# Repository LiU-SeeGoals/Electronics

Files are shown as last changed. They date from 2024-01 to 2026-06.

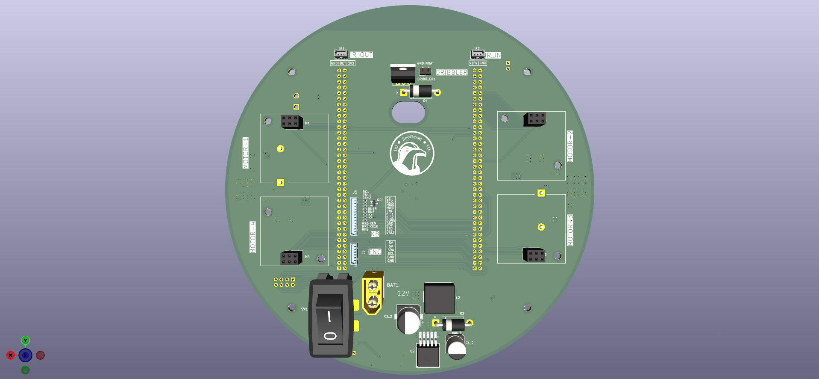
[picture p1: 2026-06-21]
pwr_v3/Docs and Images/3dRenders/pwr_v3_3dB.png

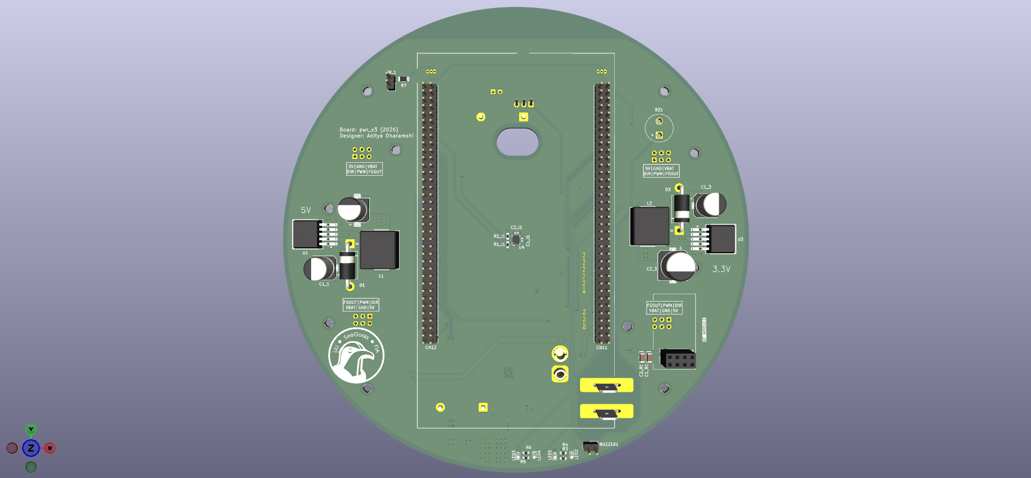
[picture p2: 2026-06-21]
pwr_v3/Docs and Images/3dRenders/pwr_v3_3dT.png

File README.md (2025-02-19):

# Electronics
Schematics etc.

# Motor driver

The motor driver has 5 important pins, 

Motor driver has 5 pins to the devboard, 2 power pins and 8 pins to the motor 

The important pins are
```
PWM, - Takes PWM signal to decide speed of motor, generate from devboard with timers.

FGOUT, - Hall sensor tick output, work like a wheel encoder and ticking as the motor spins so that we know how much the motor has spun.

nFault, - Gives fault messages when fault states are entered by going low. Currently does not work, set this pin HIGH 5v or motor driver can enter test mode.

brake - HIGH sets all motor coils high breaking the motor hard.

dir - Decides direction for motor
```

## Motor driver improvements

Capacitors and components change capacitance, inductance, etc as the voltage changes. 
This was not know during the making of driver.

Capacitors should be closer to the pins they are filtering.

There is a risk of overheating if the motors get stuck for a longer time, adding some cooling would be nice.

## Getting started

Add the .pretty library file to get footprints from lib/

Using kicad: preferences -> Manage footprint libraries

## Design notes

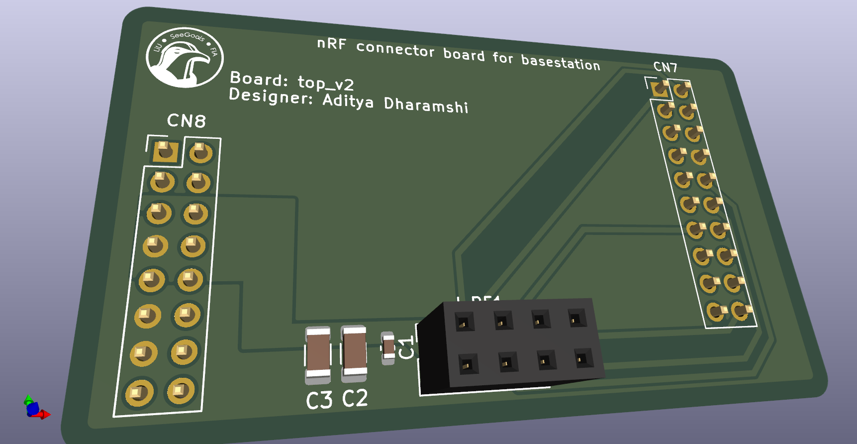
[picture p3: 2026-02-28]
top_v2/Docs and Images/top_v2_3dT2.png

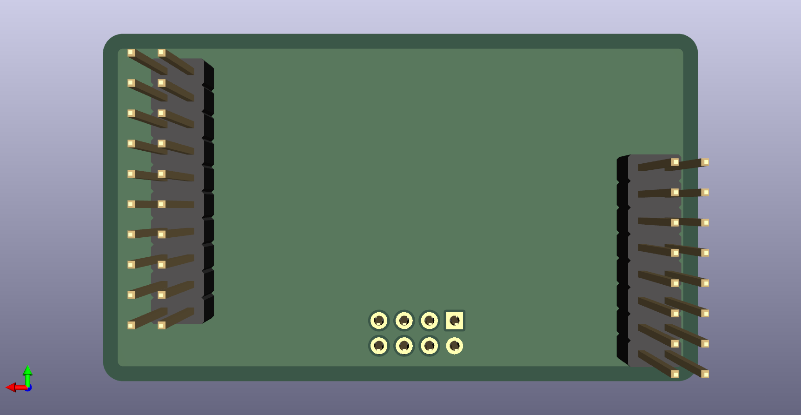
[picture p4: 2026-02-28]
top_v2/Docs and Images/top_v2_3dB.png

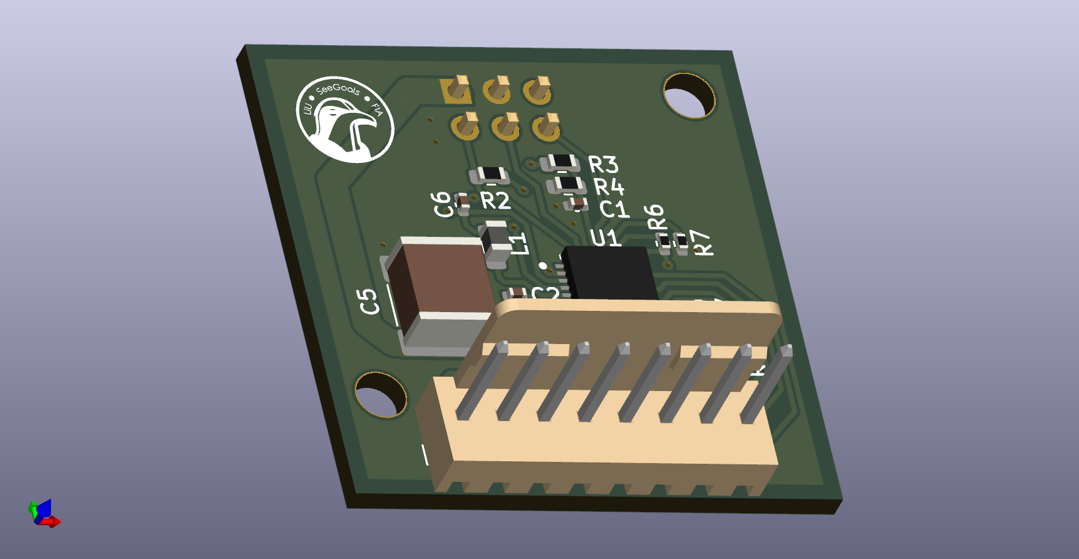
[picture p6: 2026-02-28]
md_v1/Docs and Images/md_v1_3dT2.png

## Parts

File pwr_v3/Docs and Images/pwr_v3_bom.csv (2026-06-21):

Value | Reference | Footprint | Description
Conn_01x02 | IR_1 | Connector_PinHeader_2.54mm:PinHeader_1x02_P2.54mm_Vertical | C27985187
Conn_01x02 | BUZZER1 | Connector_PinHeader_2.54mm:PinHeader_1x02_P2.54mm_Vertical | C27985187
8.2p | C1_R1 | Capacitor_SMD:C_1206_3216Metric | C3037650
Conn_02x04_Counter_Clockwise | J_RF1 | Connector_PinSocket_2.54mm:PinSocket_2x04_P2.54mm_Vertical | C2977588
D | D4 | Diode_THT:D_DO-201AD_P15.24mm_Horizontal | C2965232
1000uF | C2_1 | Capacitor_SMD:CP_Elec_8x10.5 | C2910470
LM2576S-3.3 | U3 | Package_TO_SOT_SMD:TO-263-5_TabPin3 | C2863400
LM2576S-5 | U1 | Package_TO_SOT_SMD:TO-263-5_TabPin3 | C880552
100uH | L1,L3 | Inductor_SMD:L_Sunlord_MWSA1206S-101 | C408533
1000uF | C2_2,C2_3 | Capacitor_SMD:CP_Elec_10x10.5 | C401766
150uH | L2 | Inductor_SMD:L_TaiTech_TMPC1265_13.5x12.5mm | C357258
100nF | C1_I1 | Capacitor_SMD:C_0402_1005Metric | C307331
1k | R2_I1 | Resistor_SMD:R_0603_1608Metric | C161809
1k | R1_I1 | Resistor_SMD:R_0603_1608Metric | C161809
100uF | C1_1,C1_2,C1_3 | Capacitor_SMD:CP_Elec_8x10 | C116241
XT60 | BAT1 | Connector_AMASS:AMASS_XT60-M_1x02_P7.20mm_Vertical | C98733
Buzzer | BZ1 | Buzzer_9mm_P5_D1p95:Buzzer_9mm_P5_D1p95 | C96102
Conn_02x03_Counter_Clockwise | M1,M2,M3,M4 | Connector_PinSocket_2.54mm:PinSocket_2x03_P2.54mm_Vertical | C92272
BSS84 | Q2 | Package_TO_SOT_SMD:SOT-23 | C82079
BUK9832-55A | Q1 | Package_TO_SOT_THT:TO-220-3_Vertical | C38774
10k | RK9,RK10 | Resistor_SMD:R_0402_1005Metric | C25531
100 | RK1,RK5,RK6,RK7,RK8,RK11,RK12,RK13 | Resistor_SMD:R_0402_1005Metric | C25076
62 | R3 | Resistor_SMD:R_0603_1608Metric | C23222
16.2 | R4,R6 | Resistor_SMD:R_0603_1608Metric | C22811
15.4 | R5 | Resistor_SMD:R_0603_1608Metric | C22805
100 | R7 | Resistor_SMD:R_1206_3216Metric | C242479
LM2576S-12 | U2 | Package_TO_SOT_SMD:TO-263-5_TabPin3 | C16671
1N5821 | D1,D2,D3 | Diode_THT:D_DO-201AD_P15.24mm_Horizontal | C9119
WHITE LED | LED3 | LED_SMD:LED_0603_1608Metric | C2290
BLUE LED | LED2,LED4 | LED_SMD:LED_0603_1608Metric | C2288
RED LED | LED1 | LED_SMD:LED_0603_1608Metric | C2286
100nF | C2_I1 | Capacitor_SMD:C_0402_1005Metric | C307331
LSM6DSLTR | U4 | lsm6dsltr:LGA-14_3x2.5mm_P0.5mm_LayoutBorder3x4y | C126672
10uF | C2_R1 | Capacitor_SMD:C_1206_3216Metric | C1849

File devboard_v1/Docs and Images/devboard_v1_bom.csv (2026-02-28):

Designator | Footprint | Quantity | Value | LCSC Part #
C1, C10, C16, C27, C30, C31 | 402 | 6 | 4.7uF | C23733
C11 | 402 | 1 | 1uF | C1525
C12, C13, C14, C15, C17, C18, C19, C2, C20, C21, C22, C23, C3, C4, C5, C6, C7, C8, C9 | 402 | 19 | 100nF | C14445
C24, C25, C26 | 402 | 3 | 2.2uF | C107369
C28, C29 | 402 | 2 | 10uF | C315248
D1 | 603 | 1 | LED | C2286
IC1 | SON95P300X300X100-7N-D | 1 | ST1L05CPU33R | C2969933
R1 | 402 | 1 | 62 | C412968
R2 | 402 | 1 | 10k | C71617
R3 | 402 | 1 | 100k | C191569
SW1 | TPS645-5NC105_JLCPCB | 1 | CK_KMS2xxG | C19191549
U1 | LQFP-144_20x20mm_P0.5mm | 1 | STM32H755ZITx | C730212

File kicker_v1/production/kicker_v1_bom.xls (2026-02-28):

Comment | Designator | Footprint | JLCPCB Part#(optional)
R1206 | R19 | R1206 | C873620
C1210 | C12,C13,C15,C16,C17 | C1206 | C13585
SMD | C11 | SMD | C178594
R0603 | R6,R8,R10,R20 | R0603 | C402972
R1206 | R21,R22 | R1206 | C17903
R1206 | R14 | R1206 | C17963
R0603 | R9,R13 | R0603 | C403101
R0603 | R2,R11,R15 | R0603 | C98220
R0603 | R1,R4,R12,R17 | R0603 | C22548
SOIC8N | Q1 | SOIC8N | C455164
CHIP-LED0603 | LED1 | CHIP-LED0603 | C6848499
L0603 | L2,L4,L5 | L0603 | C14709
SOIC8N | IC8 | SOIC8N | C903505
SOIC8N | IC6 | SOIC8N | C7377
SOT23 | IC4 | SOT23 | C150830
MSOP8 | IC3 | MSOP8 | C2861303
1206 | F1 | 1206 | C3163312
SMB | D2,D3 | SMB | C135043
SMC | D1 | SMC | C241736
C0805 | C21 | C0805 | C1710
C0603 | C20,C24,C25 | C0603 | C3833060
C0603 | C6,C7,C8,C9,C10,C18,C19,C22,C27 | C0603 | C1591
DF13-12P-1.25V | X1 | DF13C-12P-1.25V | C5340794
0R008 | R18 | R1206 | C912775
4R7 | R16 | R0805 | C278658
IKB40N65ES5 | Q2,Q3 | D2PAK | C536153
rd | LED2 | CHIP-LED0603 | C6784992
MCP1790 | IC10 | SOT223 | C511289
LT3751FE | IC7 | TSSOP20P | C580130
SI8620EC-B-IS | IC1 | SOIC8N | C7424691
DSEP40-03AS-TRL | D4,D5 | D2PAK | C17389077

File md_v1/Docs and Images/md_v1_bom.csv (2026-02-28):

Reference | Value | Footprint | Description
C1 | 100nF | Capacitor_SMD:C_0402_1005Metric | C1525
C2 | 47nF | Capacitor_SMD:C_0402_1005Metric | C307339
C3 | 1uF | Capacitor_SMD:C_0402_1005Metric | C14445
C4 | 0u1F | Capacitor_SMD:C_0402_1005Metric | C307331
C5 | 22uF | Capacitor_SMD:C_2220_5750Metric | C784103
C6 | 22uF | Capacitor_SMD:C_0402_1005Metric | C105226
C7 | 1uF | Capacitor_SMD:C_0402_1005Metric | C76999
L1 | 47uH | Inductor_SMD:L_0805_2012Metric | C105499
POWER1 | Conn_02x03_Odd_Even | Connector_PinHeader_2.54mm:PinHeader_2x03_P2.54mm_Vertical | C7430399
R1 | 5k1 | Resistor_SMD:R_0603_1608Metric | C403509
R2 | 5k1 | Resistor_SMD:R_0603_1608Metric | C403509
R3 | 27k | Resistor_SMD:R_0603_1608Metric | C22967
R4 | 20k | Resistor_SMD:R_0603_1608Metric | C4184
R5 | 1M | Resistor_SMD:R_0805_2012Metric | C107700
R6 | 47k | Resistor_SMD:R_0402_1005Metric | C25792
R7 | 22k | Resistor_SMD:R_0402_1005Metric | C25547
U1 | MCT8316Z0TRGFR | MotorDriver:RGF0040E-IPC_A | C3681342

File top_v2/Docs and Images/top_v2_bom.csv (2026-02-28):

Designator | Footprint | Quantity | Value | LCSC Part #
C1 | 603 | 1 | 8.2pF | C71660
C2 | 1206 | 1 | 0.1uF | C2981728
C3 | 1206 | 1 | 10uF | C696375

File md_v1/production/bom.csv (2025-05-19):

Designator | Footprint | Quantity | Value | LCSC Part #
C1 | 0402 | 1 | 100nF
C2 | 0402 | 1 | 47nF
C3, C7 | 0402 | 2 | 1uF
C4 | 0402 | 1 | 0u1F
C5 | 2220 | 1 | 22uF
C6 | 0402 | 1 | 22uF
L1 | 0805 | 1 | 47uH
MH1, MH2 |  | 2
R1, R2 | 0603 | 2 | 5k1
R3 | 0603 | 1 | 27k
R4 | 0603 | 1 | 20k
R5 | 0805 | 1 | 1M
R6 | 0402 | 1 | 47k
R7 | 0402 | 1 | 22k
U1 | RGF0040E-IPC_A | 1 | MCT8316Z0TRGFR

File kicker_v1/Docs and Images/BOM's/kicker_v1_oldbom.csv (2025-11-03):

Reference | Value | Footprint | Qty | Digi-Key | Mfg Part #
R19 | 10M | Kicking Device v13b:R1206 | 1 | 541-10MBACT-ND
C23,C26 | 1800u | Kicking Device v13b:EB35D | 2 | 493-7224-ND
C12,C13,C15,C16,C17 | 10u | Kicking Device v13b:C1210 | 5 | 1276-6736-2-ND | C3225X5R1H106M250AB
C11 | 220u | Kicking Device v13b:PANASONIC_F | 1 | PCE5025CT-ND | EEEFT1H221AP
R6,R8,R10,R20 | 133k | Kicking Device v13b:R0603 | 4 | P133KDBCT-ND
X1 | DF13-12P-1.25V | Kicking Device v13b:DF13C-12P-1.25V | 1 | H121957CT-ND
R21,R22 | 10 | Kicking Device v13b:R1206 | 2
R18 | 0R008 | Kicking Device v13b:R1206 | 1 | RHM.008ALCT-ND
R16 | 4R7 | Kicking Device v13b:R0805 | 1 | RHM4.7KCT-ND
R14 | 24 | Kicking Device v13b:R1206 | 1
R9,R13 | 24k9 | Kicking Device v13b:R0603 | 2 | P24.9KHCT-ND
R2,R11,R15 | 10k | Kicking Device v13b:R0603 | 3 | 311-10.0KHRCT-ND
R1,R4,R12,R17 | 1k | Kicking Device v13b:R0603 | 4 | 311-1.00KHRCT-ND
Q2,Q3 | IKB40N65ES5 | Kicking Device v13b:D2PAK | 2 | IKB40N65ES5ATMA1CT-ND
Q1 | FDS2582 | Kicking Device v13b:SOIC8N | 1 | FDS2582CT-ND
LED2 | rd | Kicking Device v13b:CHIP-LED0603 | 1 | 732-4979-1-ND
LED1 | gr | Kicking Device v13b:CHIP-LED0603 | 1 | 732-4980-1-ND
L3 | DA2034-AL | Kicking Device v13b:DA2034-AL | 1 |  | DA2034-AL
L2,L4,L5 | 120R | Kicking Device v13b:L0603 | 3 | 490-1037-1-ND
IC10 | MCP1790 | Kicking Device v13b:SOT223 | 1 | MCP1790-3302E/DB-ND
IC8 | FAN3229TMX | Kicking Device v13b:SOIC8N | 1 | FAN3229TMXCT-ND
IC7 | LT3751FE | Kicking Device v13b:TSSOP20P | 1 | LT3751EFE#PBF-ND
IC6 | MCP6002 | Kicking Device v13b:SOIC8N | 1 | MCP6002T-I/SNCT-ND
IC4 | MCP9701A | Kicking Device v13b:SOT23 | 1 | MCP9701AT-E/TTCT-ND
IC3 | ADC122S051 | Kicking Device v13b:MSOP8 | 1 | ADC122S051CIMM/NOPBCT-ND
IC1 | SI8620EC-B-IS | Kicking Device v13b:SOIC8N | 1 | 336-2062-5-ND
F1 | 8A slow | Kicking Device v13b:1206 | 1 | 507-1194-1-ND
D4,D5 | MBRB40250TG | Kicking Device v13b:D2PAK | 2 | MBRB40250TGOS-ND
D2,D3 | SMBJ13CA | Kicking Device v13b:SMB | 2 | SMBJ13CA-FDICT-ND
D1 | ES3J | Kicking Device v13b:SMC | 1 | ES3JCT-ND
C21 | 10n | Kicking Device v13b:C0805 | 1
C20,C24,C25 | 10u | Kicking Device v13b:C0603 | 3 | 490-12737-1-ND
C6,C7,C8,C9,C10,C18,C19,C22,C27 | 100n | Kicking Device v13b:C0603 | 9 | 1292-1397-1-ND

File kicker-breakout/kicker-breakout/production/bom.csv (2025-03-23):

Designator | Footprint | Quantity | Value | LCSC Part #
J1 | Molex_KK-254_AE-6410-04A_1x04_P2.54mm_Vertical | 1 | 1x04_P2.54mm
J2 | Molex_KK-254_AE-6410-08A_1x08_P2.54mm_Vertical | 1 | 1x08_P2.54mm
J3 | Hirose_DF13C_CL535-0412-6-51_1x12-1MP_P1.25mm_Vertical | 1 | DF13C_CL535-0412-6-51_1x12-1MP_P1.25mm_Vertical
Q1 | SOT-23 | 1 | BSS84
RN7A1, RN7B1, RN7C1, RN7D1, RN8A1, RN8B1, RN8C1, RN8D1 | 0805 | 8 | 100
RN9A1, RN9D1 | 0805 | 2 | 10k

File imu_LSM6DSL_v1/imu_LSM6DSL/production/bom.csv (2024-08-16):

Designator | Footprint | Quantity | Value | LCSC Part #
C1, C2 | CAP_GRM155_MUR | 2 | 100nF
D1 | 0805 | 1 | LED
J1 | PinHeader_1x02_P2.54mm_Vertical | 1 | Conn_01x02
J2 | PinHeader_1x06_P2.54mm_Vertical | 1 | Conn_01x06
R-led1 | 0603 | 1 | 470
R_scl1, R_sda1 | 1206_PAN | 2 | 1k
U1 | QFN_6DSLTR_STM | 1 | LSM6DSLTR

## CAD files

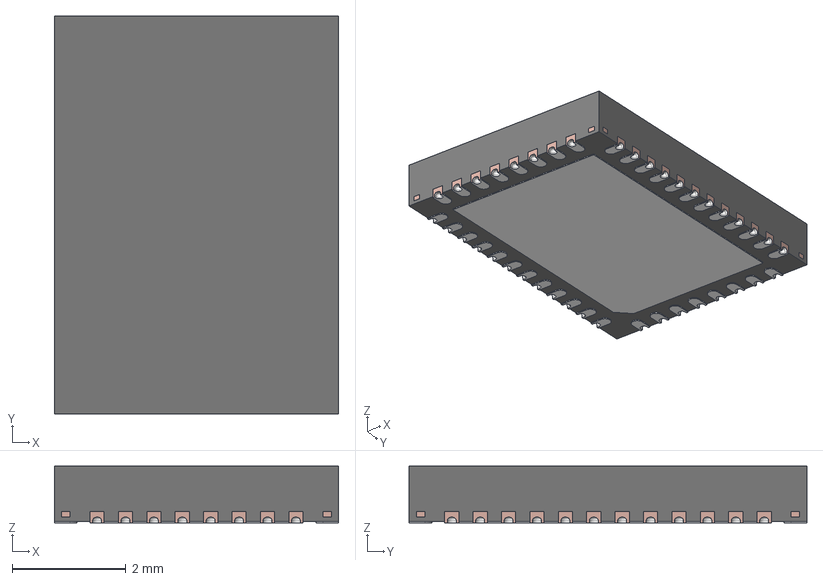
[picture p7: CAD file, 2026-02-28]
pwr_v3/libaray/motorDriver/MCT8316Z0TQRGFRQ1.stp
5.00 x 7.00 x 1.00 mm
FRAME

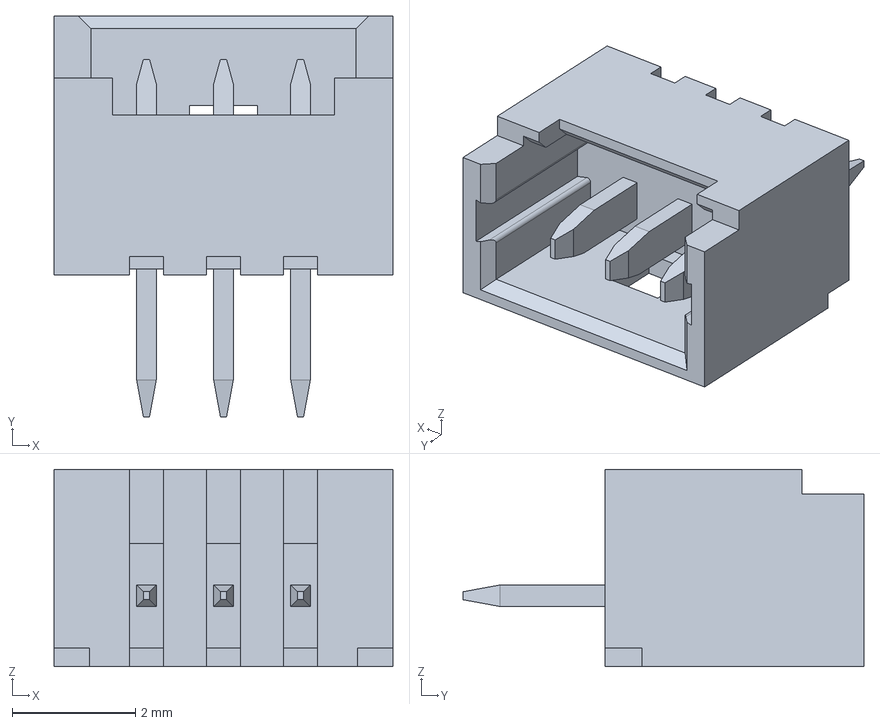
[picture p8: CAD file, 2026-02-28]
pwr_v3/libaray/picoblade_3p.stp
5.50 x 6.50 x 3.20 mm

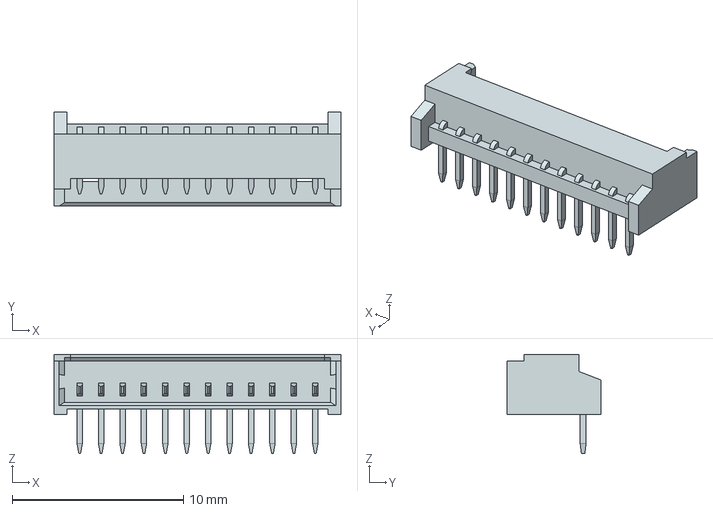
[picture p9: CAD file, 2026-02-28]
pwr_v3/libaray/picoblade_12p.stp
16.8 x 5.50 x 5.80 mm

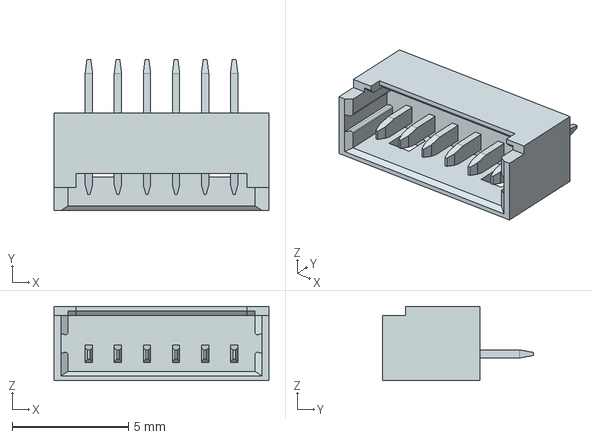
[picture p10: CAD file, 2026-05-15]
pwr_v3/libaray/530470610_6p/530470610.stp
9.25 x 6.50 x 3.20 mm

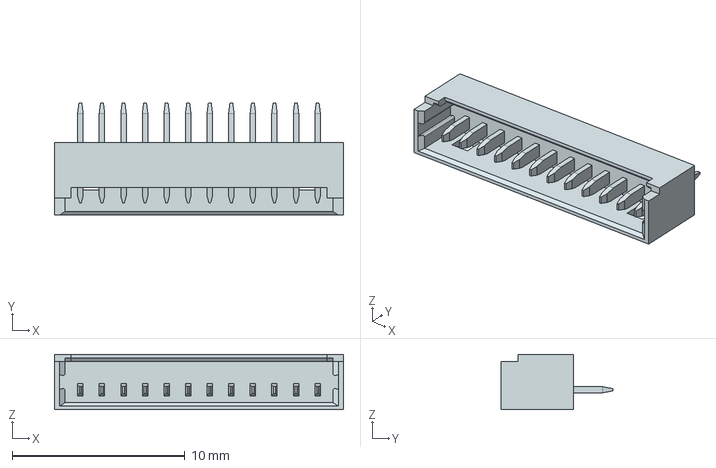
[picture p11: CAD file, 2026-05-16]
pwr_v3/libaray/530471210_12p/530471210.stp
16.8 x 6.50 x 3.20 mm

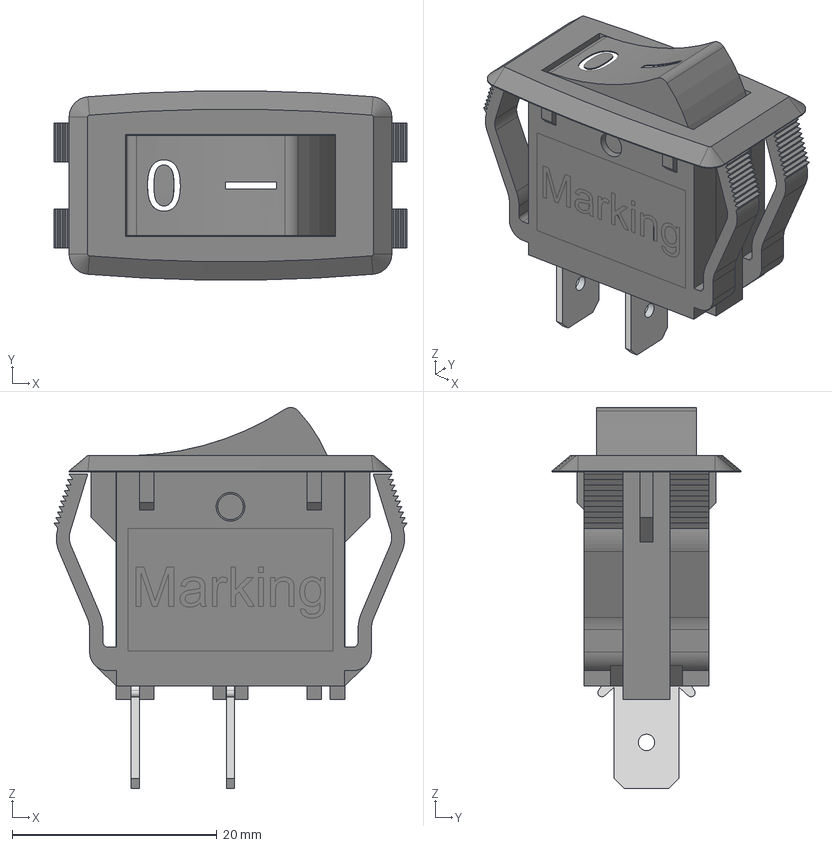
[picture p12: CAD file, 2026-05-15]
pwr_v3/libaray/Switch_471005264152/471005264152 (rev1).stp
34.5 x 18.5 x 37.2 mm
Frame
Actuator
Terminal x 2

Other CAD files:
pwr_v2/libaray/Switch_471005264152/471005264152 (rev1).stp

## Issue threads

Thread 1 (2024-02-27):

Kicker seems to be killing devboards

r0x57n, 2024-02-27:
Could be the buck converter, should have to be a list of debug steps and do some test.

r0x57n, 2024-03-28:
Got kicker up and running again on the testing board, should still make a list of debug steps to see when a board dies.

r0x57n, 2024-07-14:
seems to be working after we redid the "testboard"

Closed 2024-07-14.

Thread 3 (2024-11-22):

PCB Rev-2 modifications.

adidh4, 2024-11-22:
1. Remove the RF socket and IMU.
2. Kicker board socket and battery sockets - shift to bottom side.
3. Replace M2 with M5, and try to debug M2.
4. Add silk labels to motor driver sockets and buck convertors.
5. Increase the 0 ohm resistor sizes, probably to 1206.
6. Add mounting holes for nucleo board.
7. New locations for the robot mounting holes.
8. Add some status LED's.
9. Add new dribbler motor circuit.
10. IR sensor minor placement modification and add a current limiter resistor.

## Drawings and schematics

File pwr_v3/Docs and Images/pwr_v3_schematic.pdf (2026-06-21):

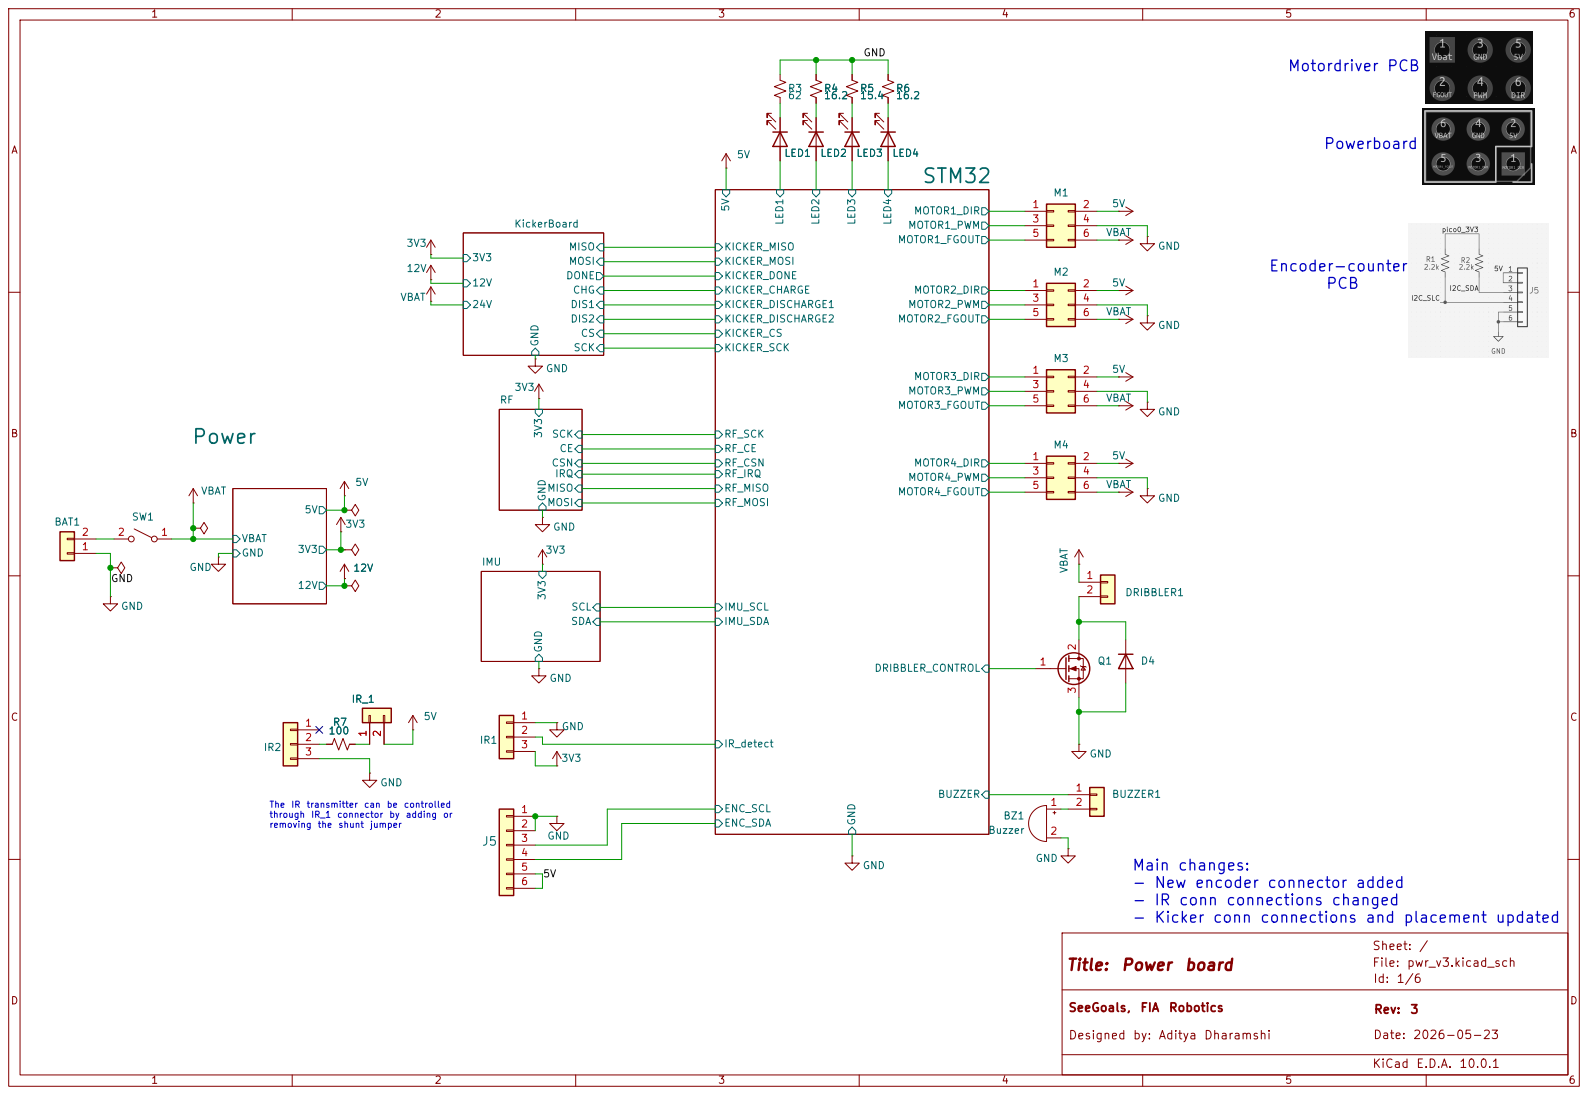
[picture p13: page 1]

SeeGoals, FIA Robotics 3V3 GND

The IR transmitter can be controlled
through IR_1 connector by adding or
removing the shunt jumper

Main changes: - New encoder connector added - IR conn connections changed - Kicker conn connections and placement updated

Designed by: Aditya Dharamshi

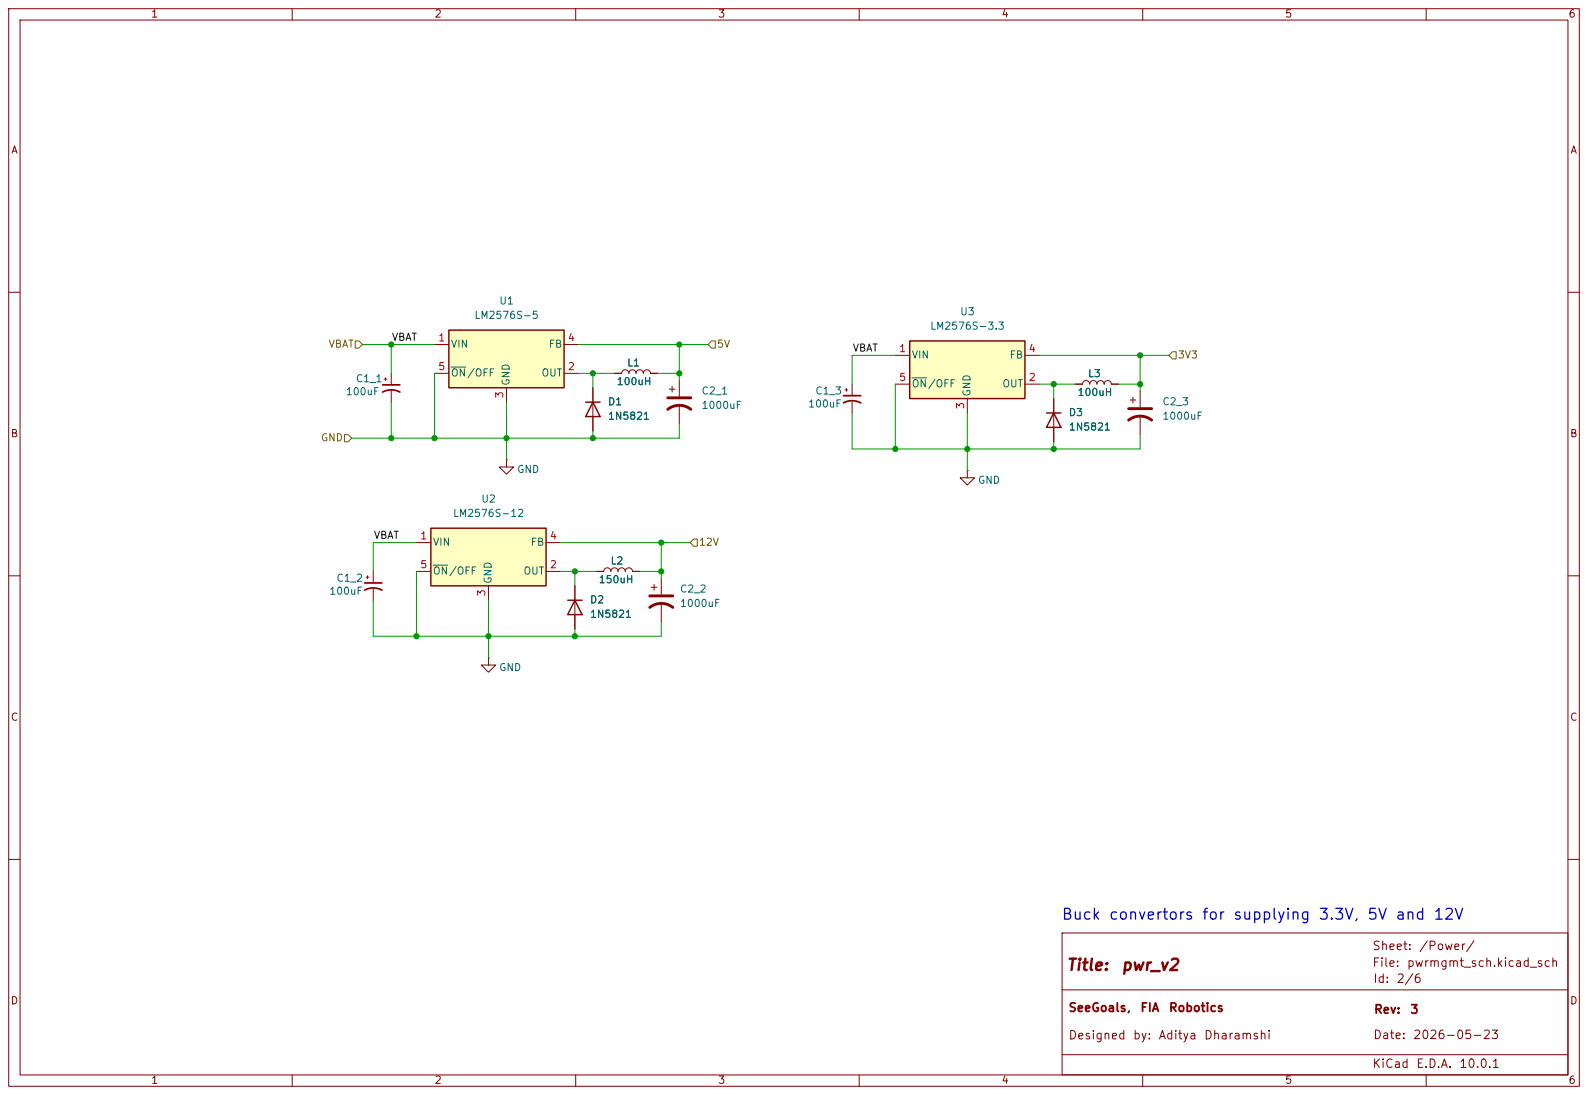
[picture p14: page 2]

Designed by: Aditya Dharamshi

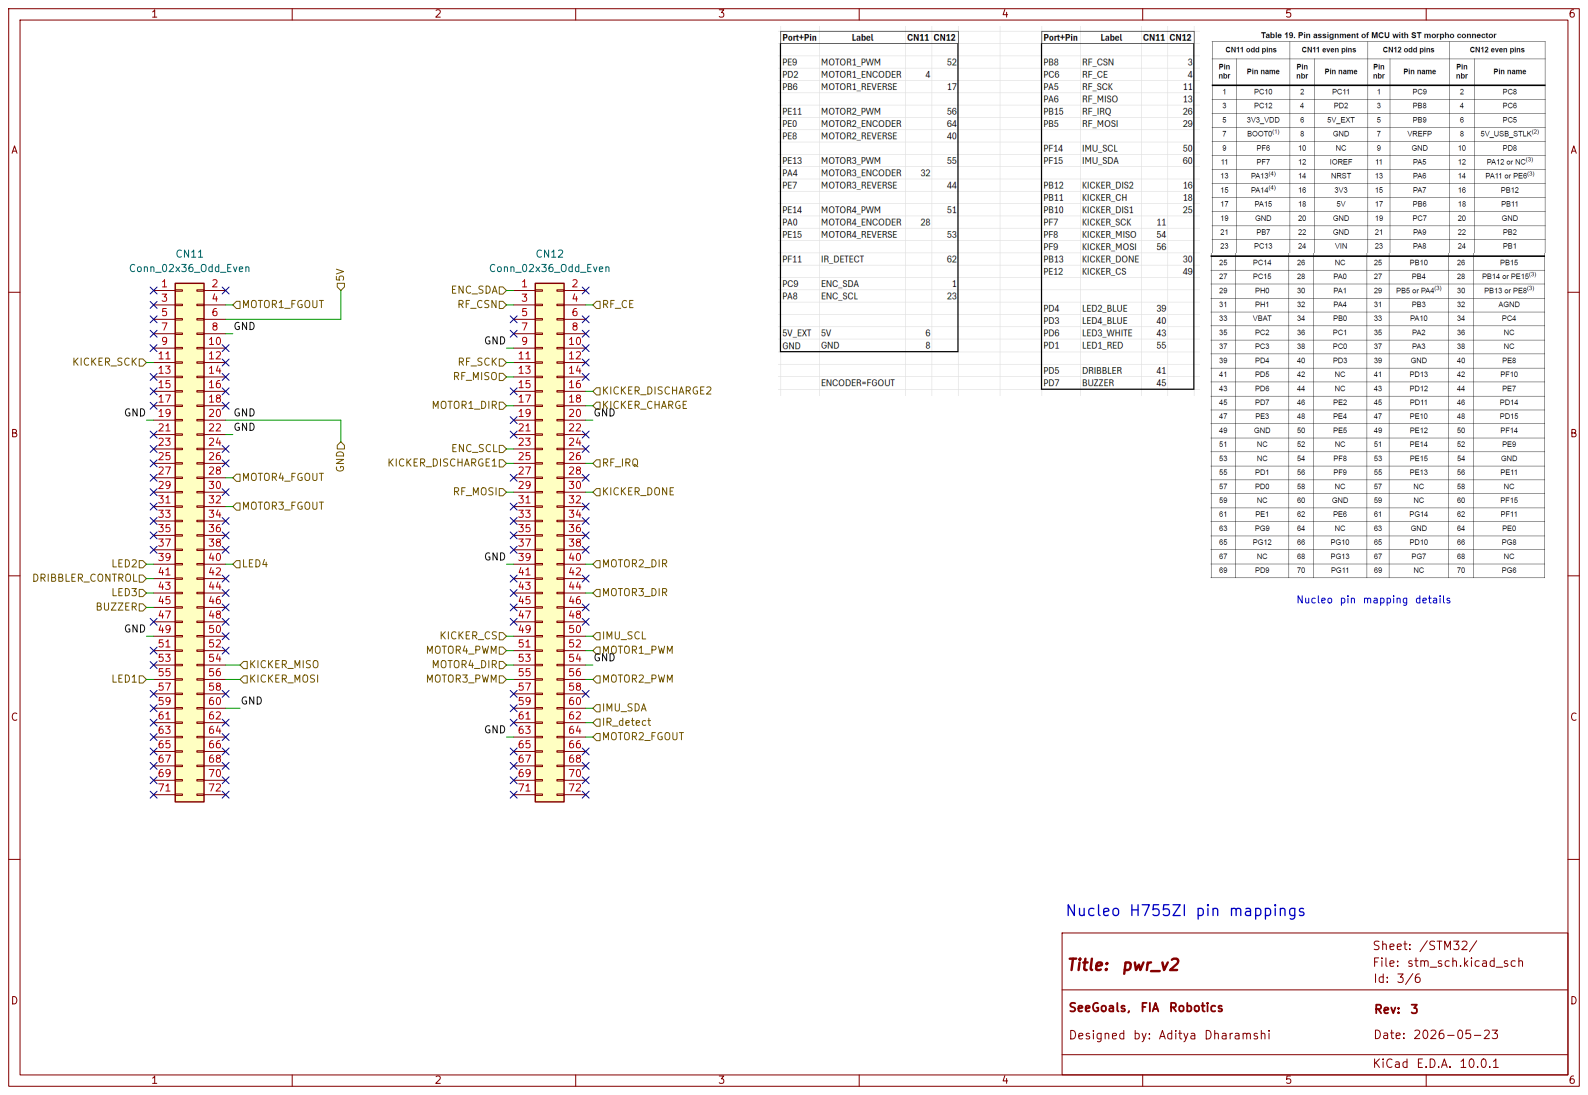
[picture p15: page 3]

Nucleo pin mapping details

Designed by: Aditya Dharamshi

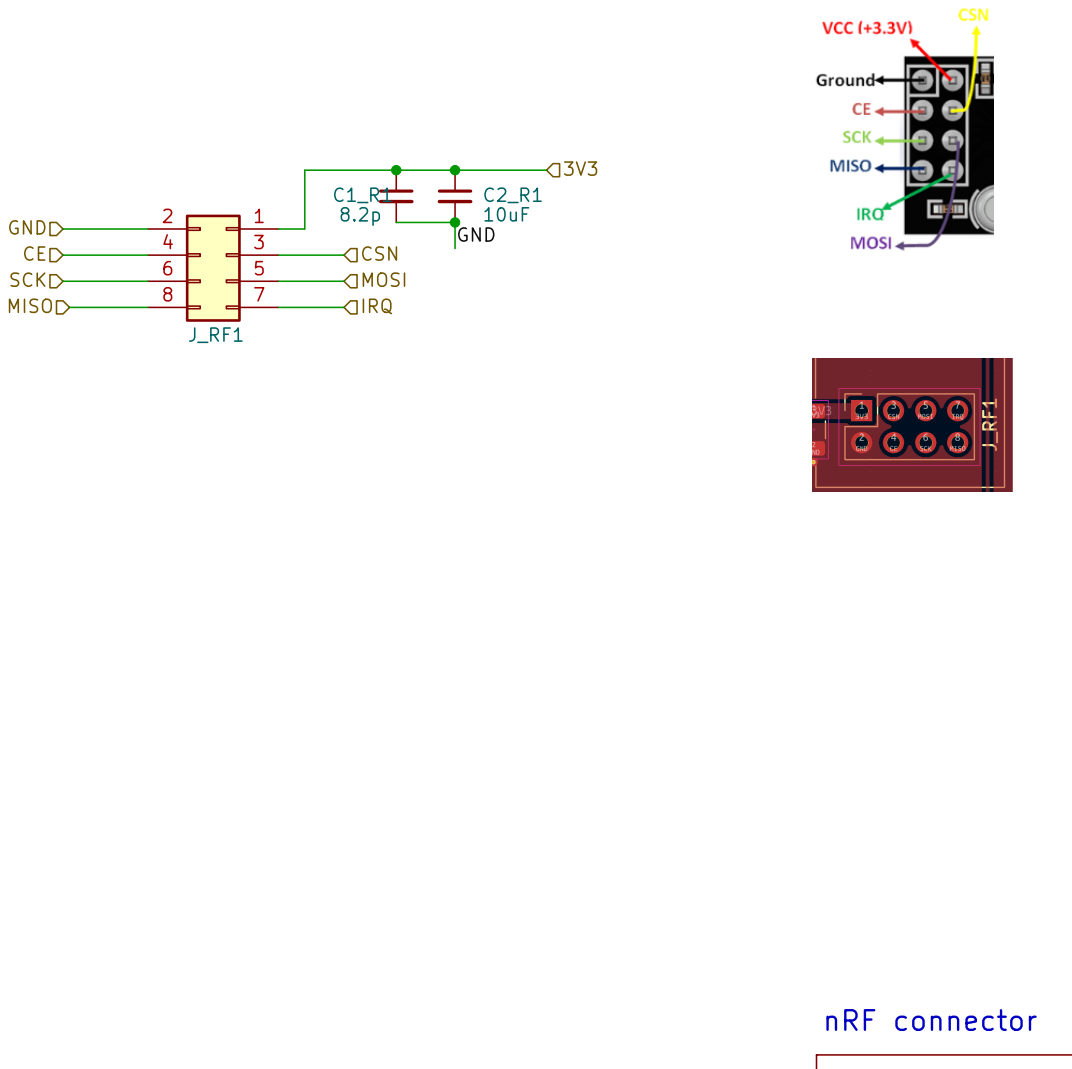
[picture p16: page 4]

Designed by: Aditya Dharamshi

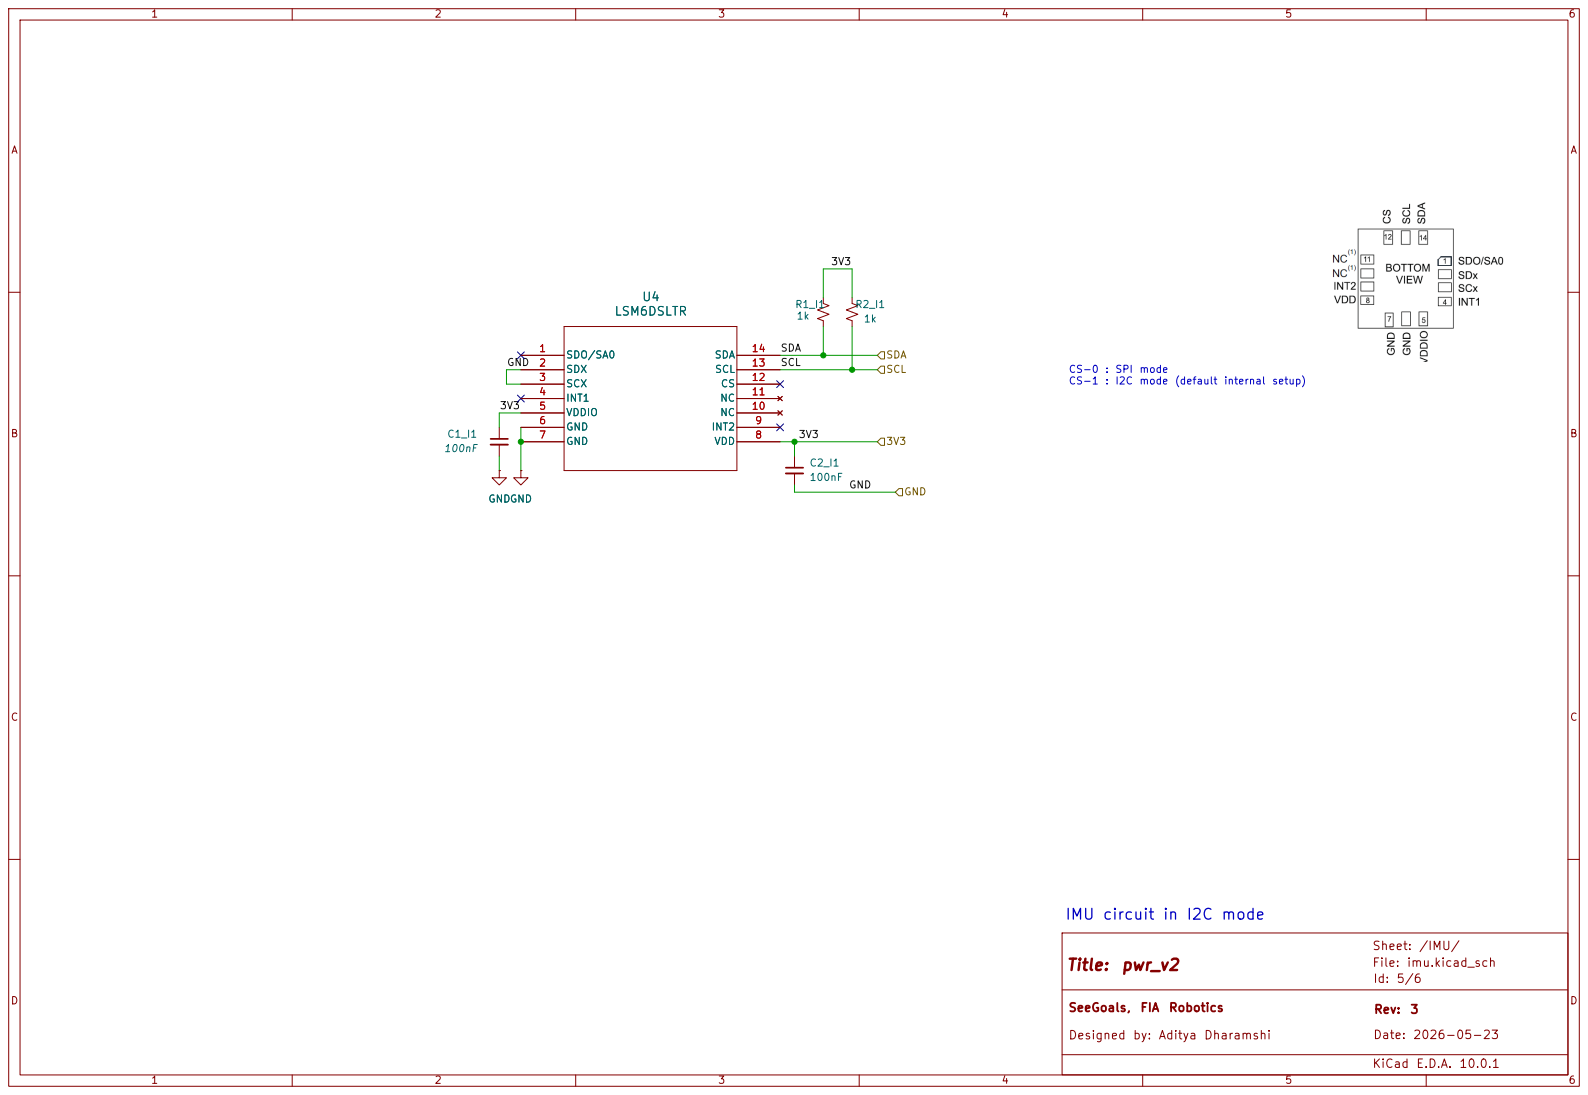
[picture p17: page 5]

CS-0 : SPI mode CS-1 : I2C mode (default internal setup)

IMU circuit in I2C mode

Designed by: Aditya Dharamshi

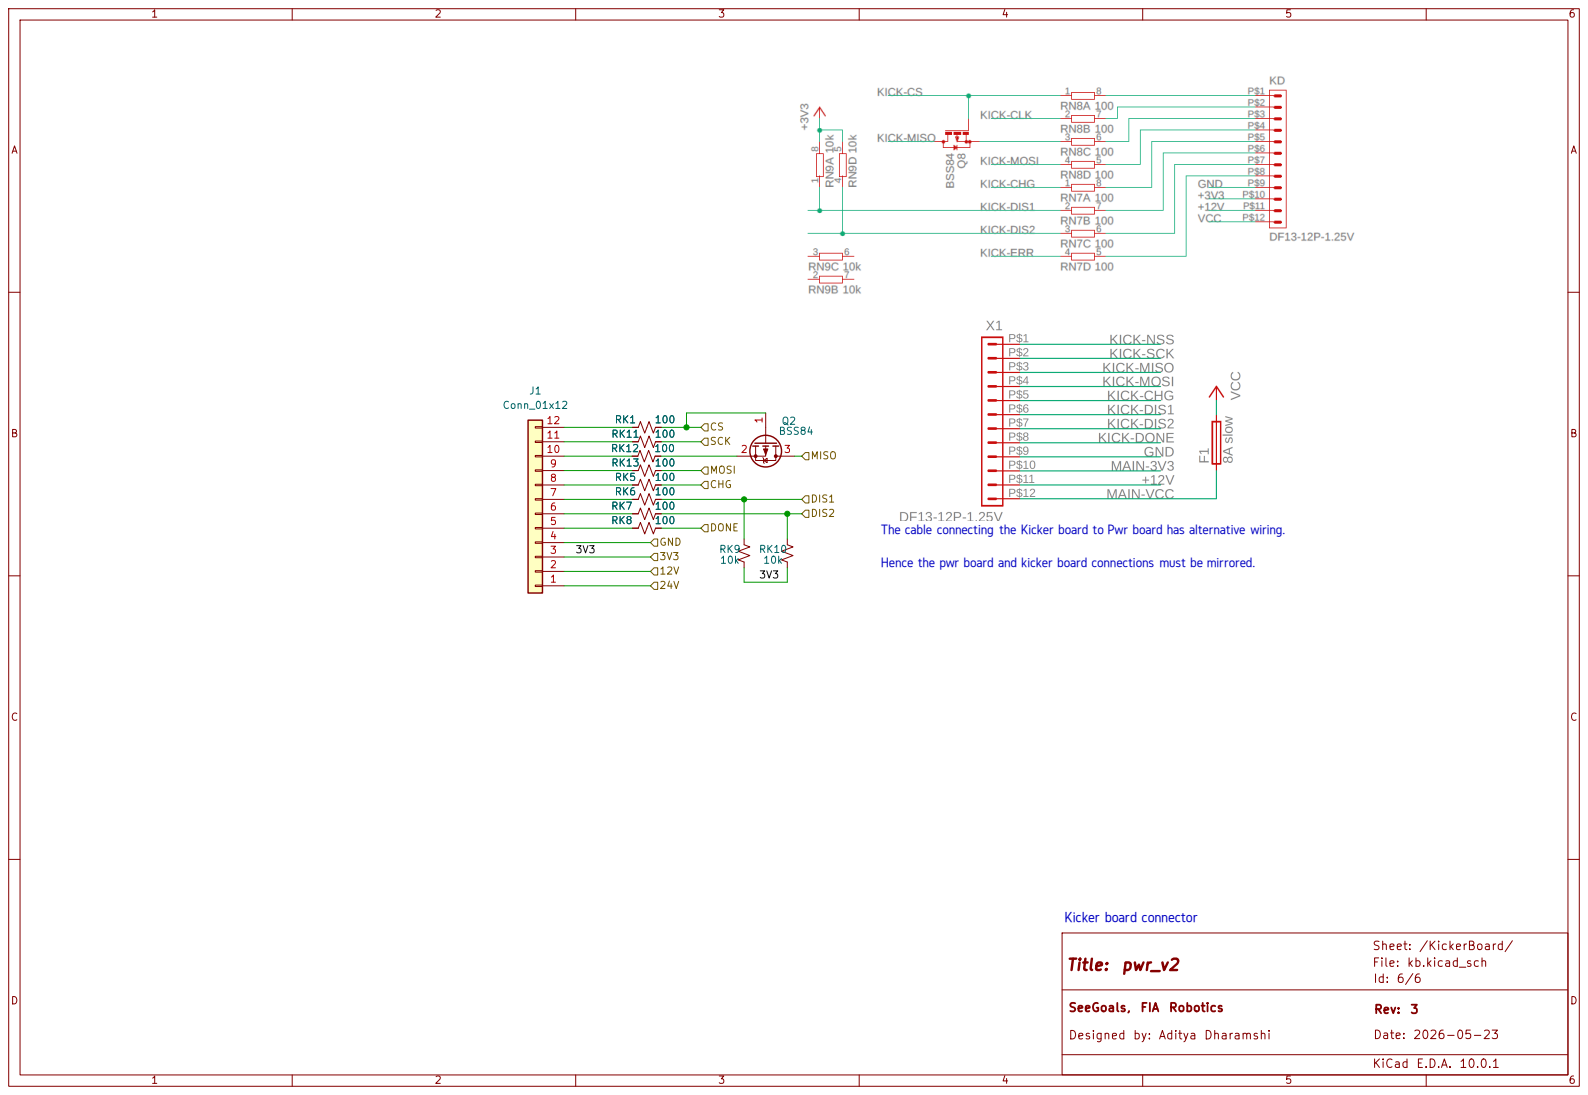
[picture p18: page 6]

The cable connecting the Kicker board to Pwr board has alternative wiring.

Designed by: Aditya Dharamshi

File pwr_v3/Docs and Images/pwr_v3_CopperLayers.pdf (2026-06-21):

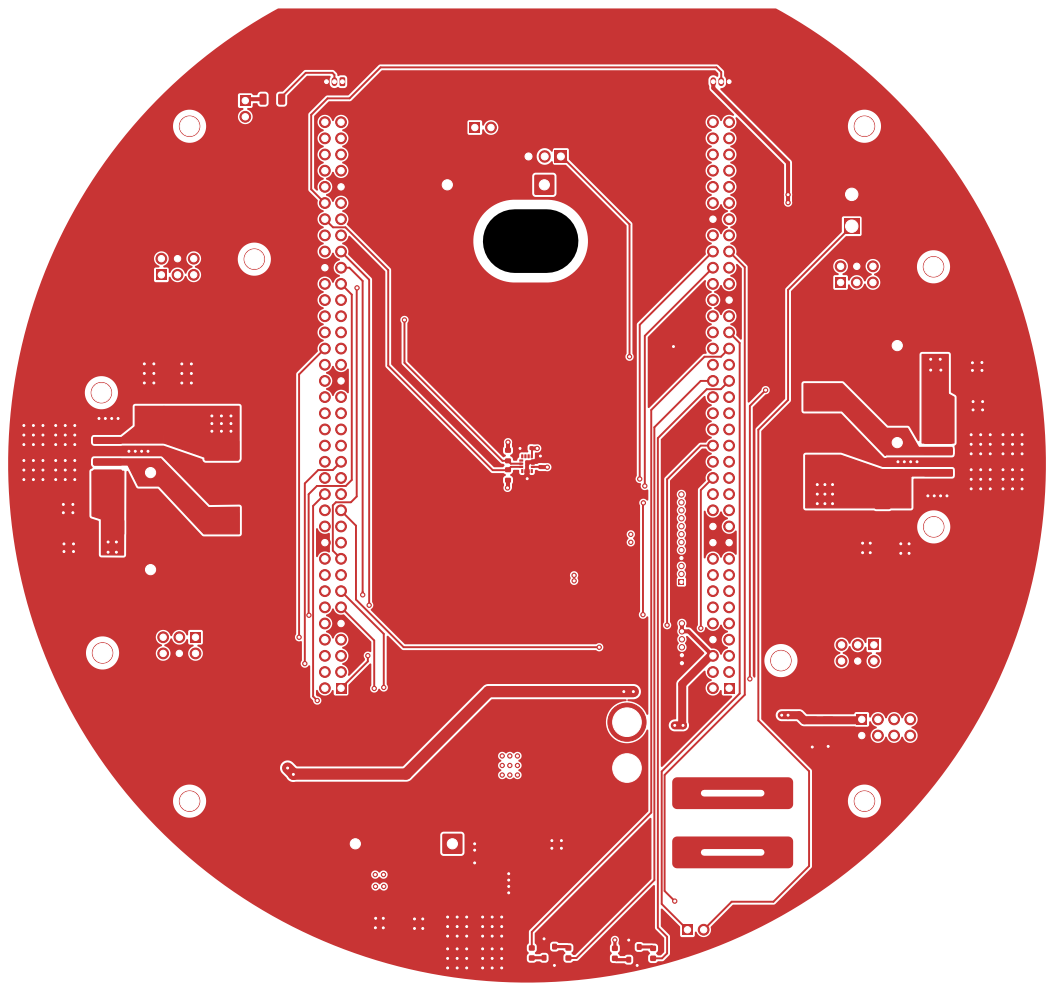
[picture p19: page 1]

Designed by: Aditya Dharamshi

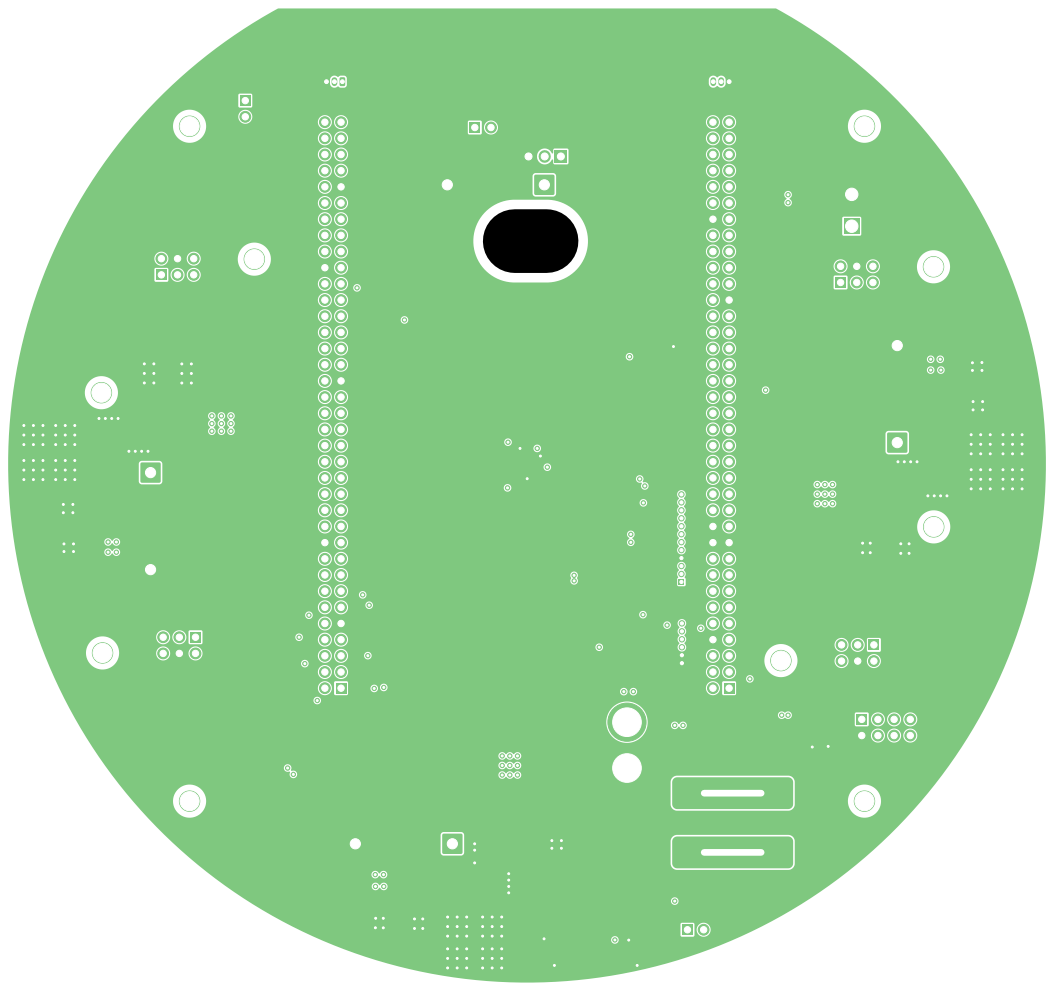
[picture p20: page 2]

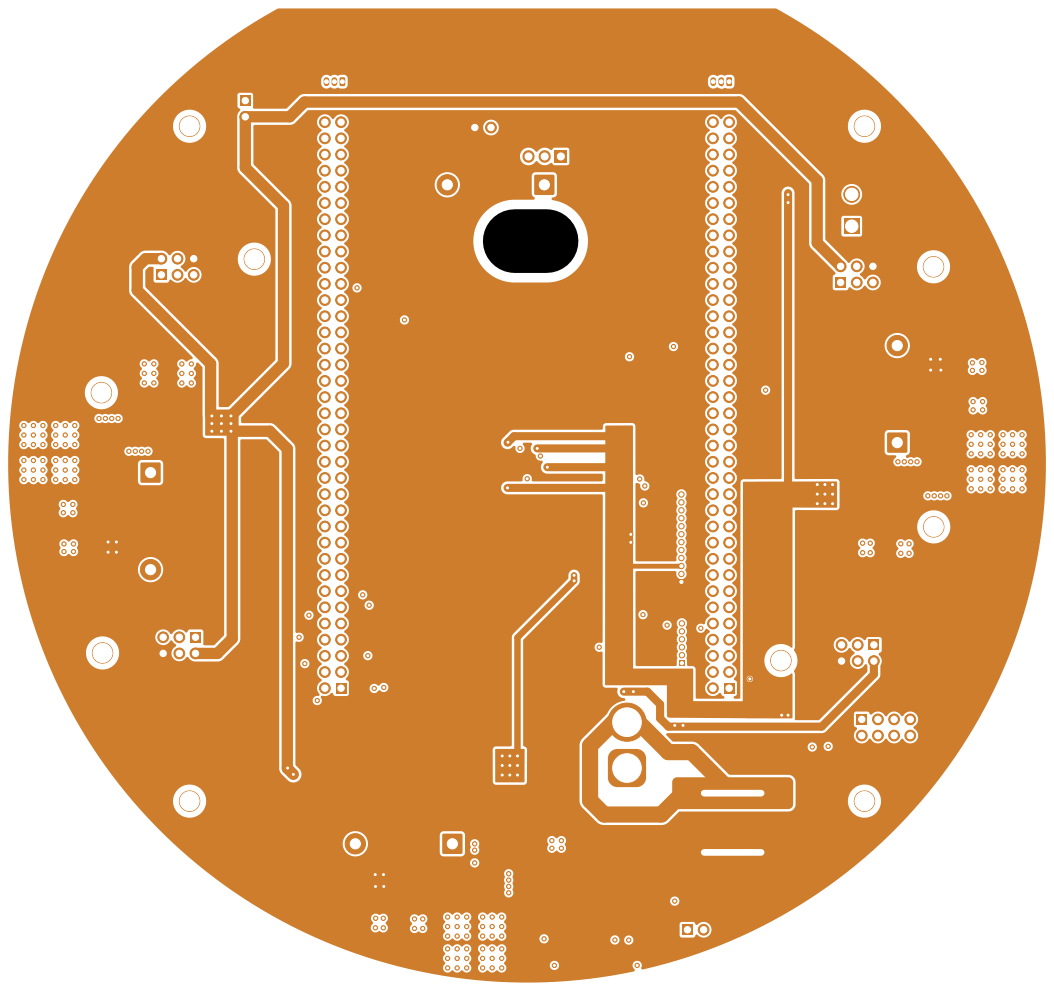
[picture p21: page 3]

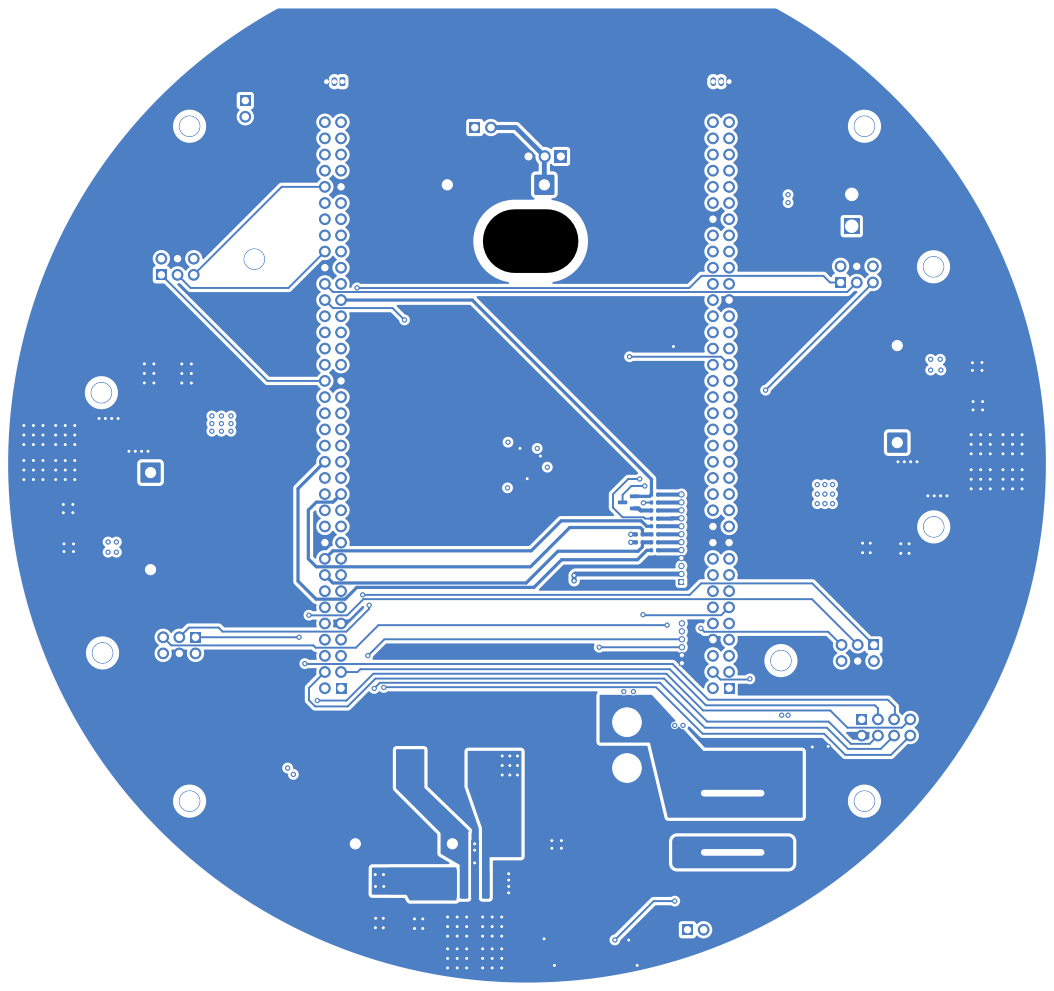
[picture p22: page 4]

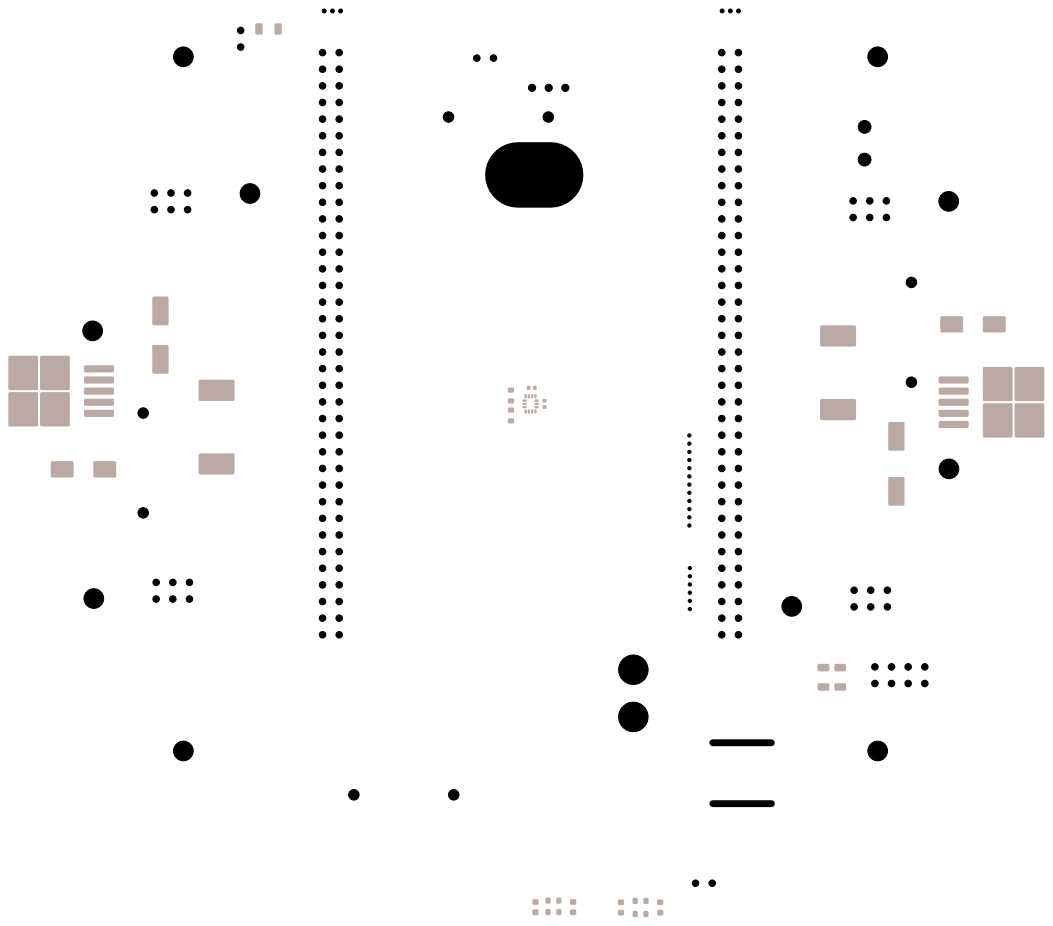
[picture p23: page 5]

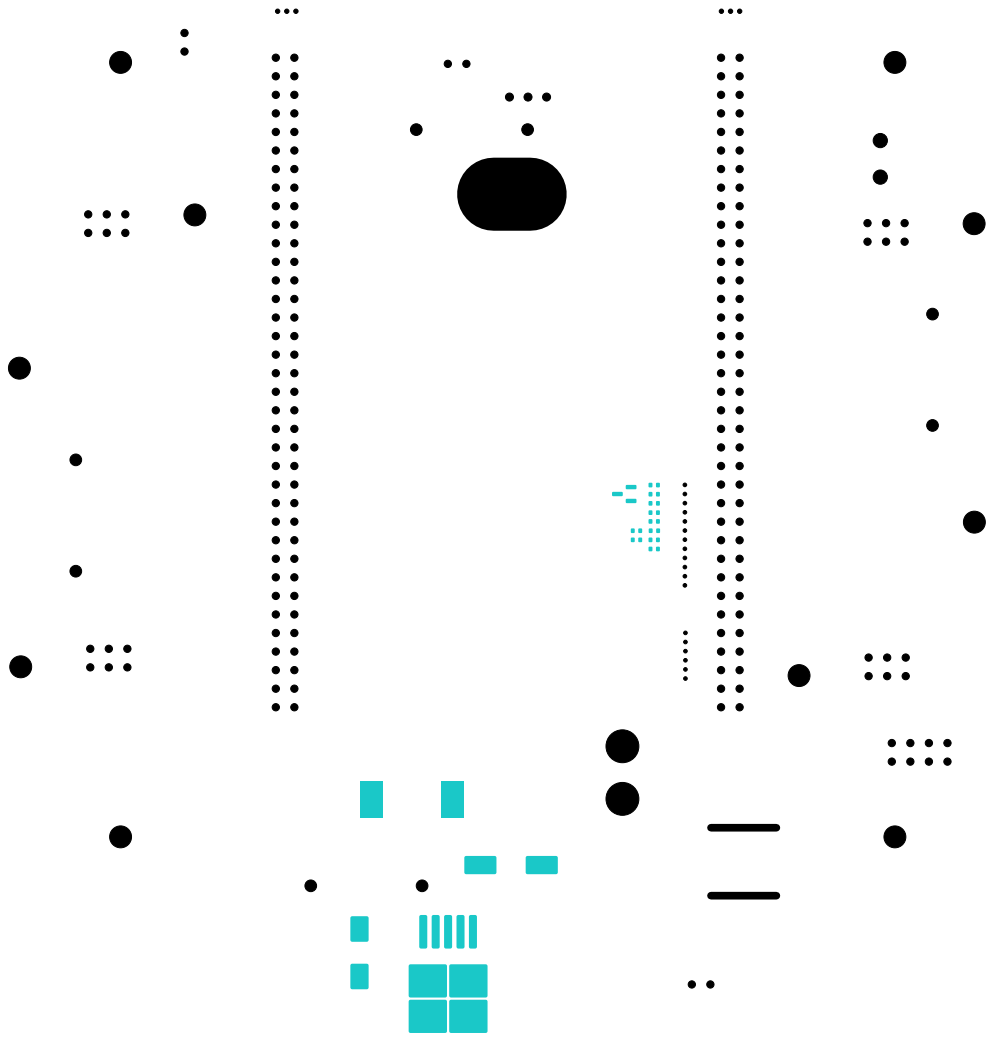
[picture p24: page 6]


FGOUT|PWM|DIR Board: pwr_v3 (2026)






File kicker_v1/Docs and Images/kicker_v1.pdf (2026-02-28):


KICK-NSS
KICK-SCK
KICK-MOSI KICK-MISO

Undervoltage:7.9V
Overvoltage(Vcc& Vtrans):disabled
Max.Cap.Voltage:244V(tested:250V)
Avg.chargecurrent:3.3A
Peakcurrent:13.25A
CAP-RAW: 3.3V@251V

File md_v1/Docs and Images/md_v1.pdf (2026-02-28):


9 AVDD 25 AGND_1 2 SW_BK 5 GND_BK 4 FB_BK 3 HPC 31 HPB 29 HPA 27 OUTA_1 13 OUTB_1 16 OUTC_1 19 U1 MCT8316Z0TRGFR

9 AVDD 25 AGND_1 2 SW_BK 5 GND_BK 4 FB_BK 3 HPC 31 HPB 29 HPA 27 OUTA_1 13 OUTB_1 16 OUTC_1 19 C4



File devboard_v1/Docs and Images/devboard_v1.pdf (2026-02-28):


6 VDD 106 VSSA 34 VDD 119 VSSSMPS 14 VDD 129 VDD 144 VDD33_USB91 VDD50_USB90 VDDA 36 VDDLDO 70 VDDLDO 105 VDDLDO 143 VDDSMPS 16 PA0 37 PA1 38 PA2 39 PA3 40 PA4 43 PA5 44 PA6 45 PA7 46 PA8 97 PA9 98 PA10 99 PA11 100 PA12 101 PA13 102 PA14 107 PA15 108 PB0 49 PB1 50 PB2 51 PB3 130 PB4 131 PB5 132 PB6 133 PB7 134 PB8 136 PB9 137 PB10 66 PB11 67 PB12 72 PB13 73 PB14 74 PB15 75 PC0 28 PC1 29 PC2_C 30 PC3_C 31 PC4 47 PC5 48 PC6 93 PC7 94 PC8 95 PC9 96 PC10 109 PC11 110 PC12 111 PC13 9 PC14 10 PC15 11 PD0 112 PD1 113 PD2 114 PD3 115 PD4 116 PD5 117 PD6 120 PD7 121 PD8 76 PD9 77 PD10 78 PD11 81 PD12 82 PD13 83 PD14 84 PD15 85 C5

6 VDD 106 VSSA 34 VDD 119 VSSSMPS 14 VDD 129 VDD 144 VDD33_USB91 VDD50_USB90 VDDA 36 VDDLDO 70 VDDLDO 105 VDDLDO 143 VDDSMPS 16 PA0 37 PA1 38 PA2 39 PA3 40 PA4 43 PA5 44 PA6 45 PA7 46 PA8 97 PA9 98 PA10 99 PA11 100 PA12 101 PA13 102 PA14 107 PA15 108 PB0 49 PB1 50 PB2 51 PB3 130 PB4 131 PB5 132 PB6 133 PB7 134 PB8 136 PB9 137 PB10 66 PB11 67 PB12 72 PB13 73 PB14 74 PB15 75 PC0 28 PC1 29 PC2_C 30 PC3_C 31 PC4 47 PC5 48 PC6 93 PC7 94 PC8 95 PC9 96 PC10 109 PC11 110 PC12 111 PC13 9 PC14 10 PC15 11 PD0 112 PD1 113 PD2 114 PD3 115 PD4 116 PD5 117 PD6 120 PD7 121 PD8 76 PD9 77 PD10 78 PD11 81 PD12 82 PD13 83 PD14 84 PD15 85 U1STM32H755ZITx

7 VDD 13 VDD 19 VDD 32 VDD 42 VDD 56 VDD 71 VDD 79 VDD 92 VSS



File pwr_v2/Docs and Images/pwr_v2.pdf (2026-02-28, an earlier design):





SCK CE GND
IRQ MOSI CSN MISO



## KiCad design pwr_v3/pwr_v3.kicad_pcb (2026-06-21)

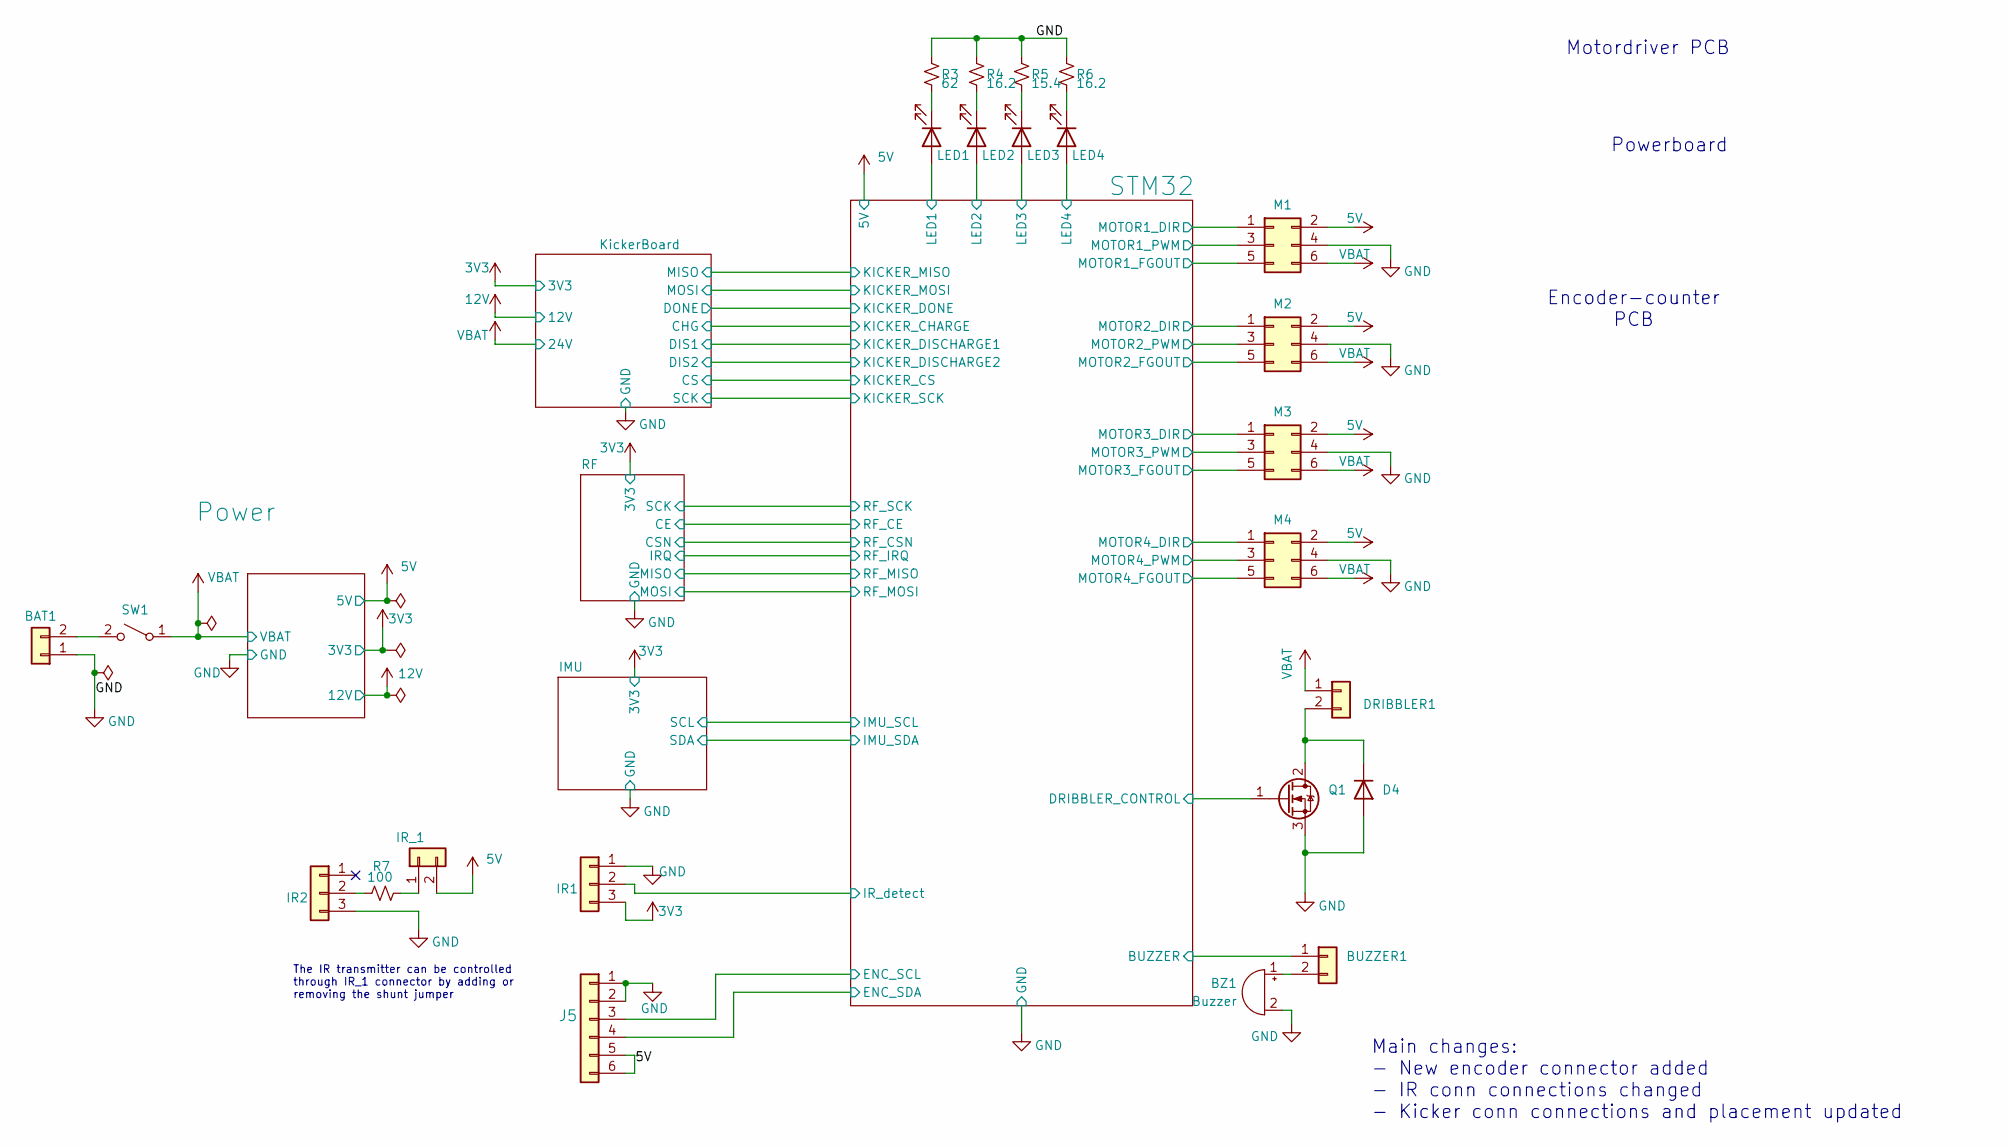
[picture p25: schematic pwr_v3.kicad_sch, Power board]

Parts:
BAT1: XT60; AMASS_XT60-M_1x02_P7.20mm_Vertical
BUZZER1: Conn_01x02; PinHeader_1x02_P2.54mm_Vertical
BZ1: Buzzer; Buzzer_9mm_P5_D1p95
D4: D; D_DO-201AD_P15.24mm_Horizontal
DRIBBLER1: Conn_01x02; PinHeader_1x02_P2.54mm_Vertical
IR1, IR2: Conn_01x03; Hirose_DF13-03P-1.25DSA_1x03_P1.25mm_Vertical
IR_1: Conn_01x02; PinHeader_1x02_P2.54mm_Vertical
J5: 530470610
LED1: RED LED; LED_0603_1608Metric
LED2, LED4: BLUE LED; LED_0603_1608Metric
LED3: WHITE LED; LED_0603_1608Metric
M1, M2, M3, M4: Conn_02x03_Counter_Clockwise; PinSocket_2x03_P2.54mm_Vertical
Q1: BUK9832-55A; TO-220-3_Vertical
R3: 62; R_0603_1608Metric
R4, R6: 16.2; R_0603_1608Metric
R5: 15.4; R_0603_1608Metric
R7: 100; R_1206_3216Metric
SW1: SW_SPST; WS-RSTV_27.6 x13.8_RockerSwitch

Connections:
3V3: IR1.3; also elsewhere on the board
5V: IR_1.2, J5.5, J5.6, M1.2, M2.2, M3.2, M4.2; also elsewhere on the board
/STM32/BUZZER: BUZZER1.1; also elsewhere on the board
/STM32/DRIBBLER_CONTROL: Q1.1 (G); also elsewhere on the board
/STM32/ENC_SCL: J5.3; also elsewhere on the board
/STM32/ENC_SDA: J5.4; also elsewhere on the board
/STM32/IR_detect: IR1.2; also elsewhere on the board
/STM32/LED1: LED1.2 (A); also elsewhere on the board
/STM32/LED2: LED2.2 (A); also elsewhere on the board
/STM32/LED3: LED3.2 (A); also elsewhere on the board
/STM32/LED4: LED4.2 (A); also elsewhere on the board
/STM32/MOTOR1_DIR: M1.1; also elsewhere on the board
/STM32/MOTOR1_FGOUT: M1.5; also elsewhere on the board
/STM32/MOTOR1_PWM: M1.3; also elsewhere on the board
/STM32/MOTOR2_DIR: M2.1; also elsewhere on the board
/STM32/MOTOR2_FGOUT: M2.5; also elsewhere on the board
/STM32/MOTOR2_PWM: M2.3; also elsewhere on the board
/STM32/MOTOR3_DIR: M3.1; also elsewhere on the board
/STM32/MOTOR3_FGOUT: M3.5; also elsewhere on the board
/STM32/MOTOR3_PWM: M3.3; also elsewhere on the board
/STM32/MOTOR4_DIR: M4.1; also elsewhere on the board
/STM32/MOTOR4_FGOUT: M4.5; also elsewhere on the board
/STM32/MOTOR4_PWM: M4.3; also elsewhere on the board
GND: BAT1.1, BZ1.2 (-), D4.2 (A), IR1.1, IR2.3, J5.1, J5.2, M1.4, M2.4, M3.4, M4.4, Q1.3 (S), R3.1, R4.1, R5.1, R6.1; also elsewhere on the board
unnamed: BAT1.2, SW1.2 (B)
unnamed: BUZZER1.2, BZ1.1 (+)
unnamed: D4.1 (K), DRIBBLER1.2, Q1.2 (D)
unnamed: IR2.2, R7.2
unnamed: IR_1.1, R7.1
unnamed: LED1.1 (K), R3.2
unnamed: LED2.1 (K), R4.2
unnamed: LED3.1 (K), R5.2
unnamed: LED4.1 (K), R6.2
VBAT: DRIBBLER1.1, M1.6, M2.6, M3.6, M4.6, SW1.1 (A); also elsewhere on the board

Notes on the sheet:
Main changes: - New encoder connector added - IR conn connections changed - Kicker conn connections and placement updated
Motordriver PCB
The IR transmitter can be controlled through IR_1 connector by adding or removing the shunt jumper
Encoder-counter PCB
Powerboard

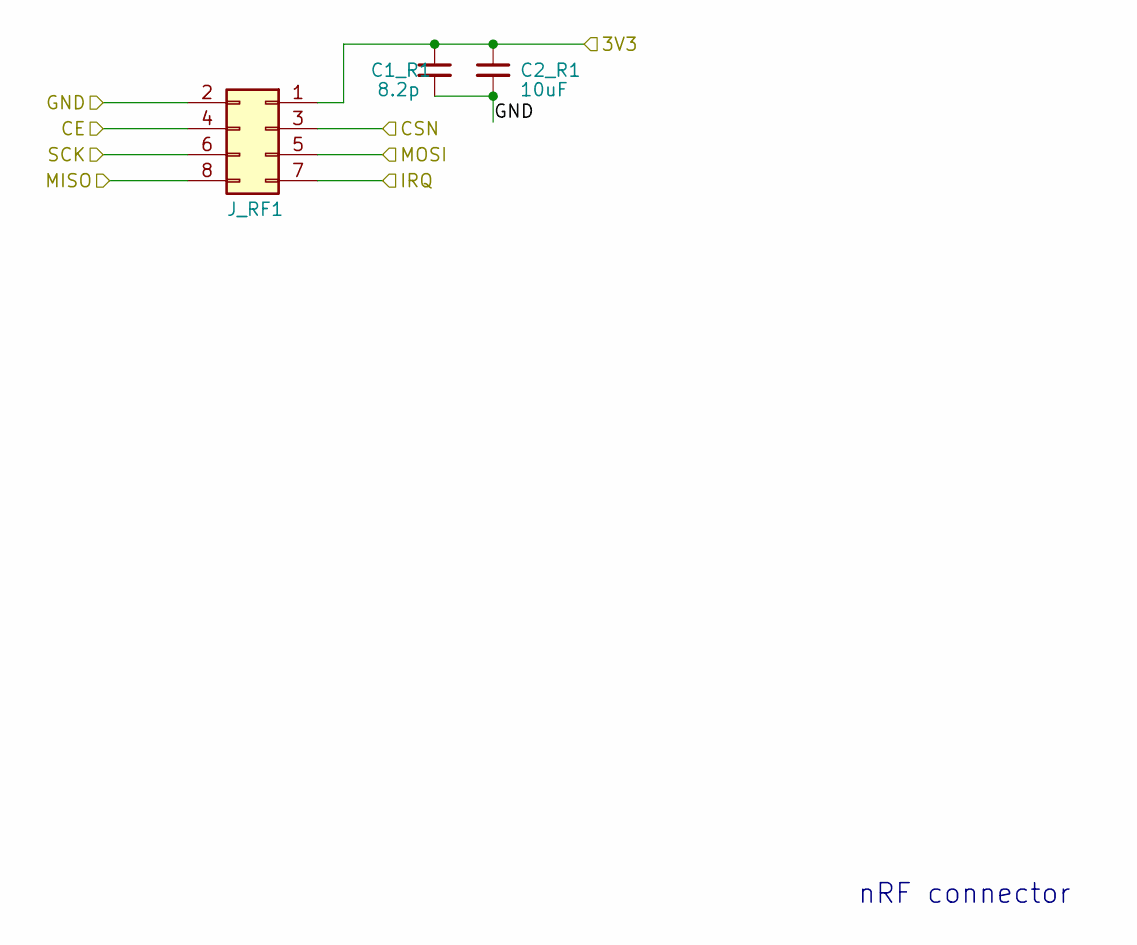
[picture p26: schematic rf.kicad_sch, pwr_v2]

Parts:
C1_R1: 8.2p; C_1206_3216Metric
C2_R1: 10uF; C_1206_3216Metric
J_RF1: Conn_02x04_Counter_Clockwise; PinSocket_2x04_P2.54mm_Vertical

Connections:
3V3: C1_R1.1, C2_R1.1, J_RF1.1; also elsewhere on the board
/RF/CE: J_RF1.4; also elsewhere on the board
/RF/CSN: J_RF1.3; also elsewhere on the board
/RF/IRQ: J_RF1.7; also elsewhere on the board
/RF/MISO: J_RF1.8; also elsewhere on the board
/RF/MOSI: J_RF1.5; also elsewhere on the board
/RF/SCK: J_RF1.6; also elsewhere on the board
GND: C1_R1.2, C2_R1.2, J_RF1.2; also elsewhere on the board

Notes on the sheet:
nRF connector

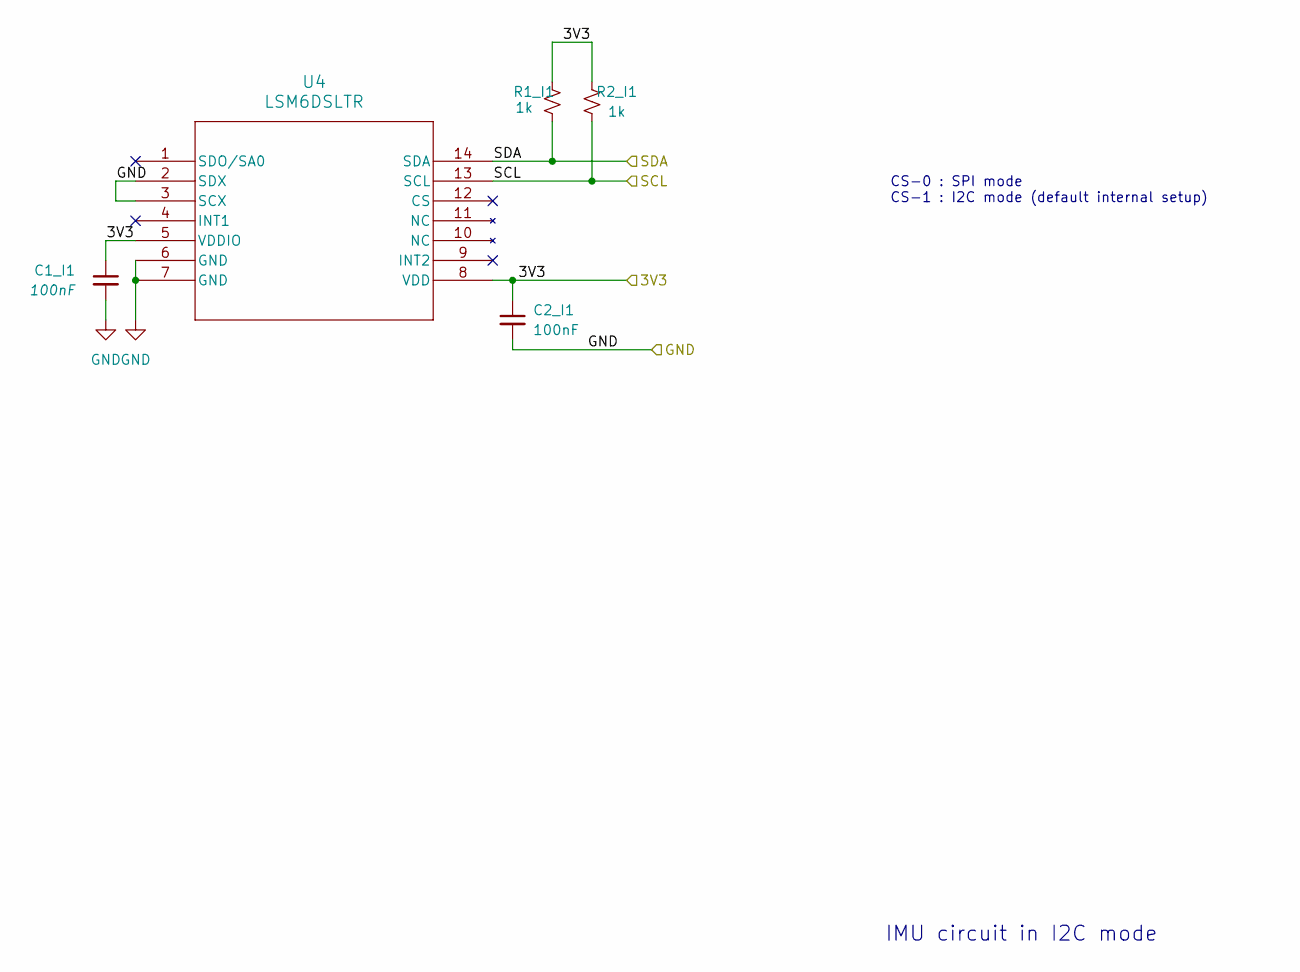
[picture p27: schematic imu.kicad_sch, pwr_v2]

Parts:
C1_I1, C2_I1: 100nF; C_0402_1005Metric
R1_I1, R2_I1: 1k; R_0603_1608Metric
U4: LSM6DSLTR; LGA-14_3x2.5mm_P0.5mm_LayoutBorder3x4y

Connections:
3V3: C1_I1.1, C2_I1.1, R1_I1.1, R2_I1.1, U4.5 (VDDIO), U4.8 (VDD); also elsewhere on the board
/IMU/SCL: R2_I1.2, U4.13 (SCL); also elsewhere on the board
/IMU/SDA: R1_I1.2, U4.14 (SDA); also elsewhere on the board
GND: C1_I1.2, C2_I1.2, U4.2 (SDX), U4.3 (SCX), U4.6 (GND), U4.7 (GND); also elsewhere on the board

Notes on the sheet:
IMU circuit in I2C mode
CS-0 : SPI mode CS-1 : I2C mode (default internal setup)

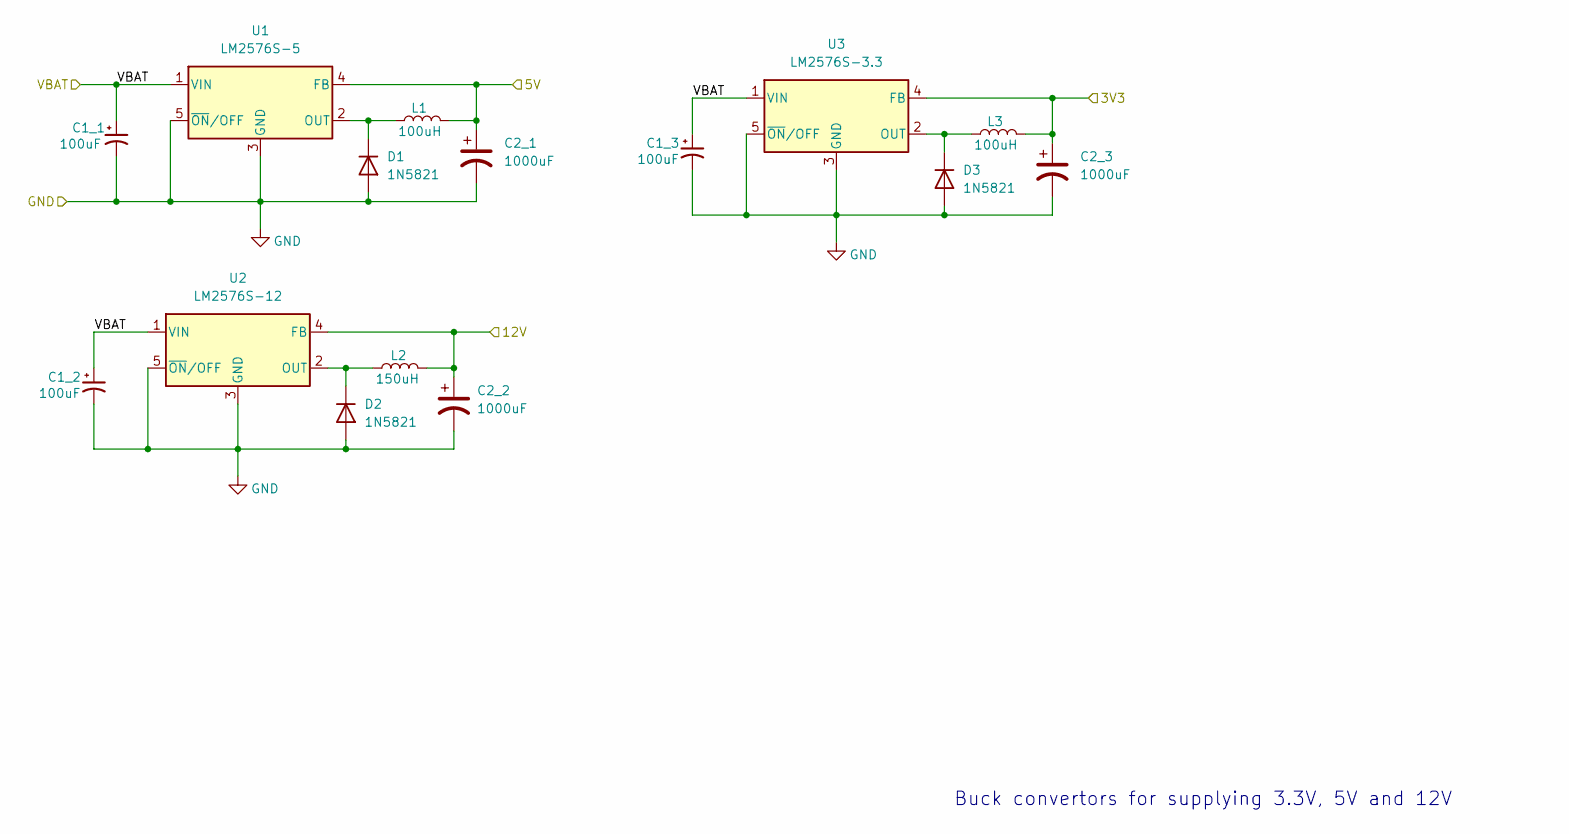
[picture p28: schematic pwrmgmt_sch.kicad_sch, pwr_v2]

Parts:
C1_1, C1_2, C1_3: 100uF; CP_Elec_8x10
C2_1: 1000uF; CP_Elec_8x10.5
C2_2, C2_3: 1000uF; CP_Elec_10x10.5
D1, D2, D3: 1N5821; D_DO-201AD_P15.24mm_Horizontal
L1, L3: 100uH; L_Sunlord_MWSA1206S-101
L2: 150uH; L_TaiTech_TMPC1265_13.5x12.5mm
U1: LM2576S-5; TO-263-5_TabPin3
U2: LM2576S-12; TO-263-5_TabPin3
U3: LM2576S-3.3; TO-263-5_TabPin3

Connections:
3V3: C2_3.1, L3.2, U3.4 (FB); also elsewhere on the board
5V: C2_1.1, L1.2, U1.4 (FB); also elsewhere on the board
12V: C2_2.1, L2.2, U2.4 (FB); also elsewhere on the board
GND: C1_1.2, C1_2.2, C1_3.2, C2_1.2, C2_2.2, C2_3.2, D1.2 (A), D2.2 (A), D3.2 (A), U1.3 (GND), U1.5 (~ON/OFF), U2.3 (GND), U2.5 (~ON/OFF), U3.3 (GND), U3.5 (~ON/OFF); also elsewhere on the board
unnamed: D1.1 (K), L1.1, U1.2 (OUT)
unnamed: D2.1 (K), L2.1, U2.2 (OUT)
unnamed: D3.1 (K), L3.1, U3.2 (OUT)
VBAT: C1_1.1, C1_2.1, C1_3.1, U1.1 (VIN), U2.1 (VIN), U3.1 (VIN); also elsewhere on the board

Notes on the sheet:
Buck convertors for supplying 3.3V, 5V and 12V

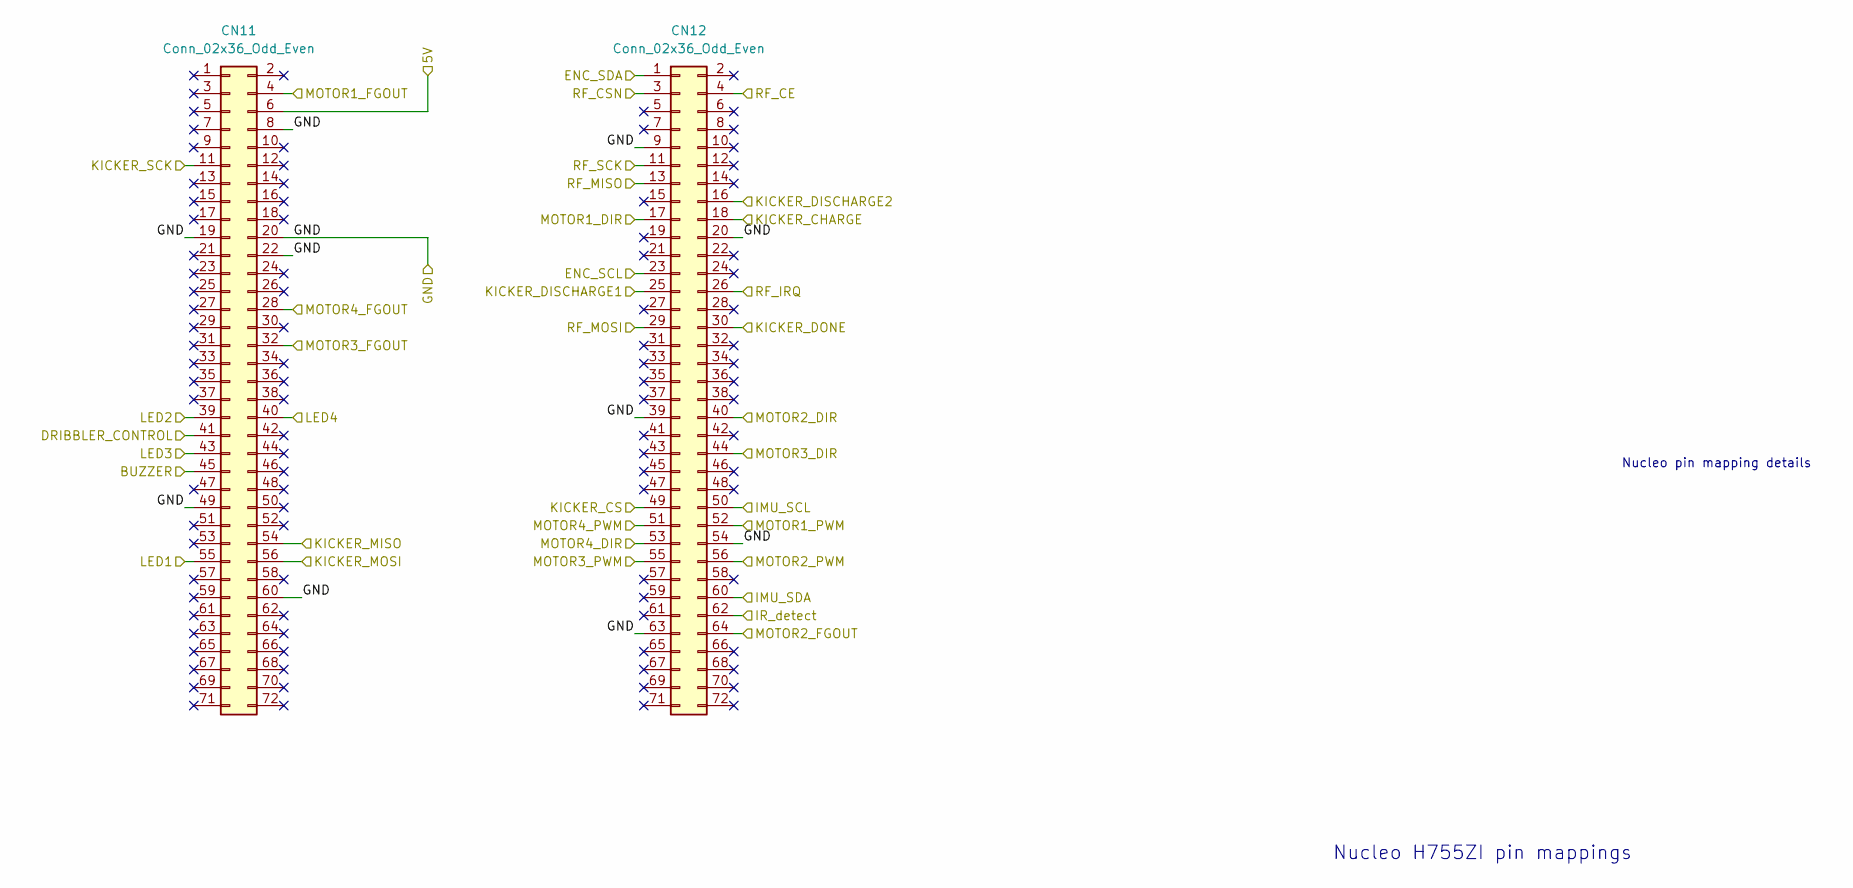
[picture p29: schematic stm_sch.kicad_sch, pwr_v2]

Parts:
CN11, CN12: Conn_02x36_Odd_Even; PinHeader_2x36_P2.54mm_Vertical

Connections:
5V: CN11.6; also elsewhere on the board
/IMU/SCL: CN12.50; also elsewhere on the board
/IMU/SDA: CN12.60; also elsewhere on the board
/KickerBoard/CHG: CN12.18; also elsewhere on the board
/KickerBoard/CS: CN12.49; also elsewhere on the board
/KickerBoard/DIS1: CN12.25; also elsewhere on the board
/KickerBoard/DIS2: CN12.16; also elsewhere on the board
/KickerBoard/DONE: CN12.30; also elsewhere on the board
/KickerBoard/MISO: CN11.54; also elsewhere on the board
/KickerBoard/MOSI: CN11.56; also elsewhere on the board
/KickerBoard/SCK: CN11.11; also elsewhere on the board
/RF/CE: CN12.4; also elsewhere on the board
/RF/CSN: CN12.3; also elsewhere on the board
/RF/IRQ: CN12.26; also elsewhere on the board
/RF/MISO: CN12.13; also elsewhere on the board
/RF/MOSI: CN12.29; also elsewhere on the board
/RF/SCK: CN12.11; also elsewhere on the board
/STM32/BUZZER: CN11.45; also elsewhere on the board
/STM32/DRIBBLER_CONTROL: CN11.41; also elsewhere on the board
/STM32/ENC_SCL: CN12.23; also elsewhere on the board
/STM32/ENC_SDA: CN12.1; also elsewhere on the board
/STM32/IR_detect: CN12.62; also elsewhere on the board
/STM32/LED1: CN11.55; also elsewhere on the board
/STM32/LED2: CN11.39; also elsewhere on the board
/STM32/LED3: CN11.43; also elsewhere on the board
/STM32/LED4: CN11.40; also elsewhere on the board
/STM32/MOTOR1_DIR: CN12.17; also elsewhere on the board
/STM32/MOTOR1_FGOUT: CN11.4; also elsewhere on the board
/STM32/MOTOR1_PWM: CN12.52; also elsewhere on the board
/STM32/MOTOR2_DIR: CN12.40; also elsewhere on the board
/STM32/MOTOR2_FGOUT: CN12.64; also elsewhere on the board
/STM32/MOTOR2_PWM: CN12.56; also elsewhere on the board
/STM32/MOTOR3_DIR: CN12.44; also elsewhere on the board
/STM32/MOTOR3_FGOUT: CN11.32; also elsewhere on the board
/STM32/MOTOR3_PWM: CN12.55; also elsewhere on the board
/STM32/MOTOR4_DIR: CN12.53; also elsewhere on the board
/STM32/MOTOR4_FGOUT: CN11.28; also elsewhere on the board
/STM32/MOTOR4_PWM: CN12.51; also elsewhere on the board
GND: CN11.8, CN11.19, CN11.20, CN11.22, CN11.49, CN11.60, CN12.9, CN12.20, CN12.39, CN12.54, CN12.63; also elsewhere on the board

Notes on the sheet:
Nucleo H755ZI pin mappings
Nucleo pin mapping details

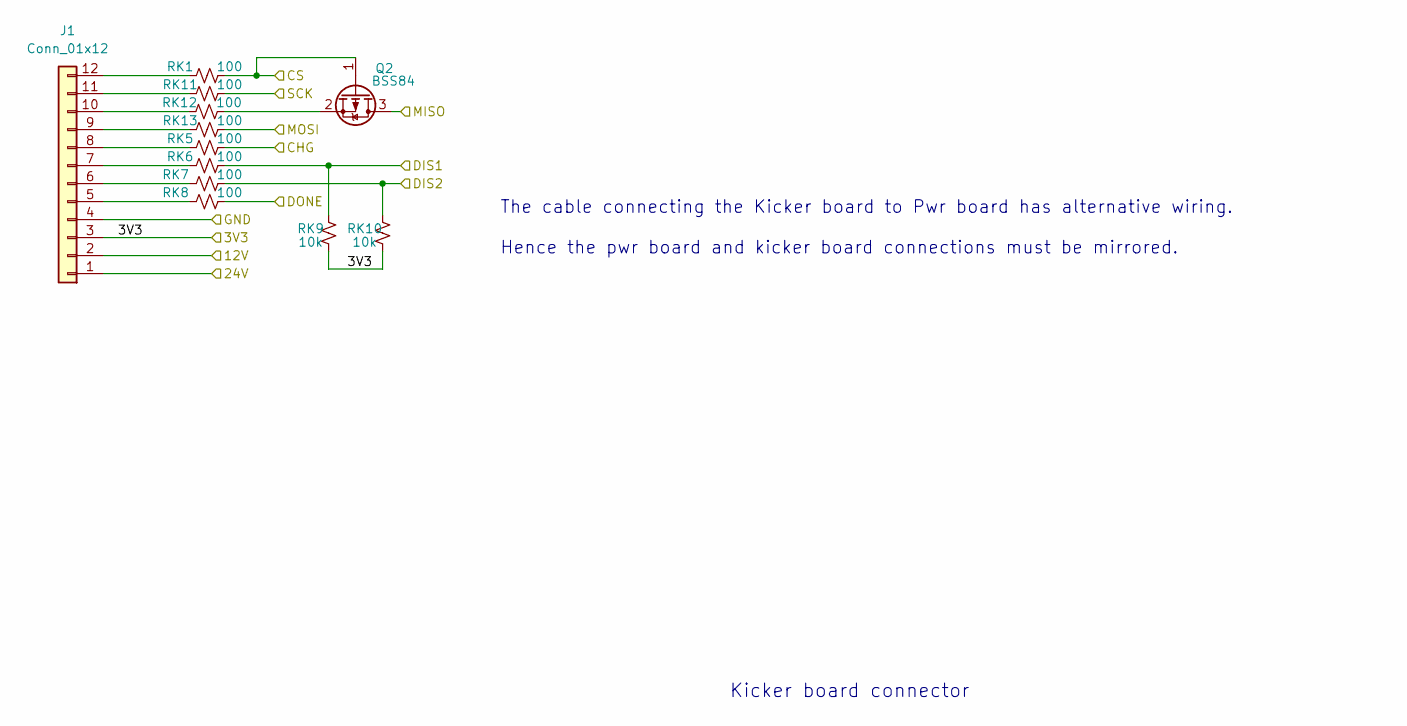
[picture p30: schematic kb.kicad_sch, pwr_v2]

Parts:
J1: Conn_01x12; 530471210
Q2: BSS84; SOT-23
RK1, RK5, RK6, RK7, RK8, RK11, RK12, RK13: 100; R_0402_1005Metric
RK9, RK10: 10k; R_0402_1005Metric

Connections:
3V3: J1.3, RK9.1, RK10.1; also elsewhere on the board
12V: J1.2; also elsewhere on the board
/KickerBoard/CHG: RK5.2; also elsewhere on the board
/KickerBoard/CS: Q2.1 (G), RK1.2; also elsewhere on the board
/KickerBoard/DIS1: RK6.2, RK9.2; also elsewhere on the board
/KickerBoard/DIS2: RK7.2, RK10.2; also elsewhere on the board
/KickerBoard/DONE: RK8.2; also elsewhere on the board
/KickerBoard/MISO: Q2.3 (D); also elsewhere on the board
/KickerBoard/MOSI: RK13.2; also elsewhere on the board
/KickerBoard/SCK: RK11.2; also elsewhere on the board
GND: J1.4; also elsewhere on the board
unnamed: J1.5, RK8.1
unnamed: J1.6, RK7.1
unnamed: J1.7, RK6.1
unnamed: J1.8, RK5.1
unnamed: J1.9, RK13.1
unnamed: J1.10, RK12.1
unnamed: J1.11, RK11.1
unnamed: J1.12, RK1.1
unnamed: Q2.2 (S), RK12.2
VBAT: J1.1; also elsewhere on the board

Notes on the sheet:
Kicker board connector
The cable connecting the Kicker board to Pwr board has alternative wiring. Hence the pwr board and kicker board connections must be mirrored.

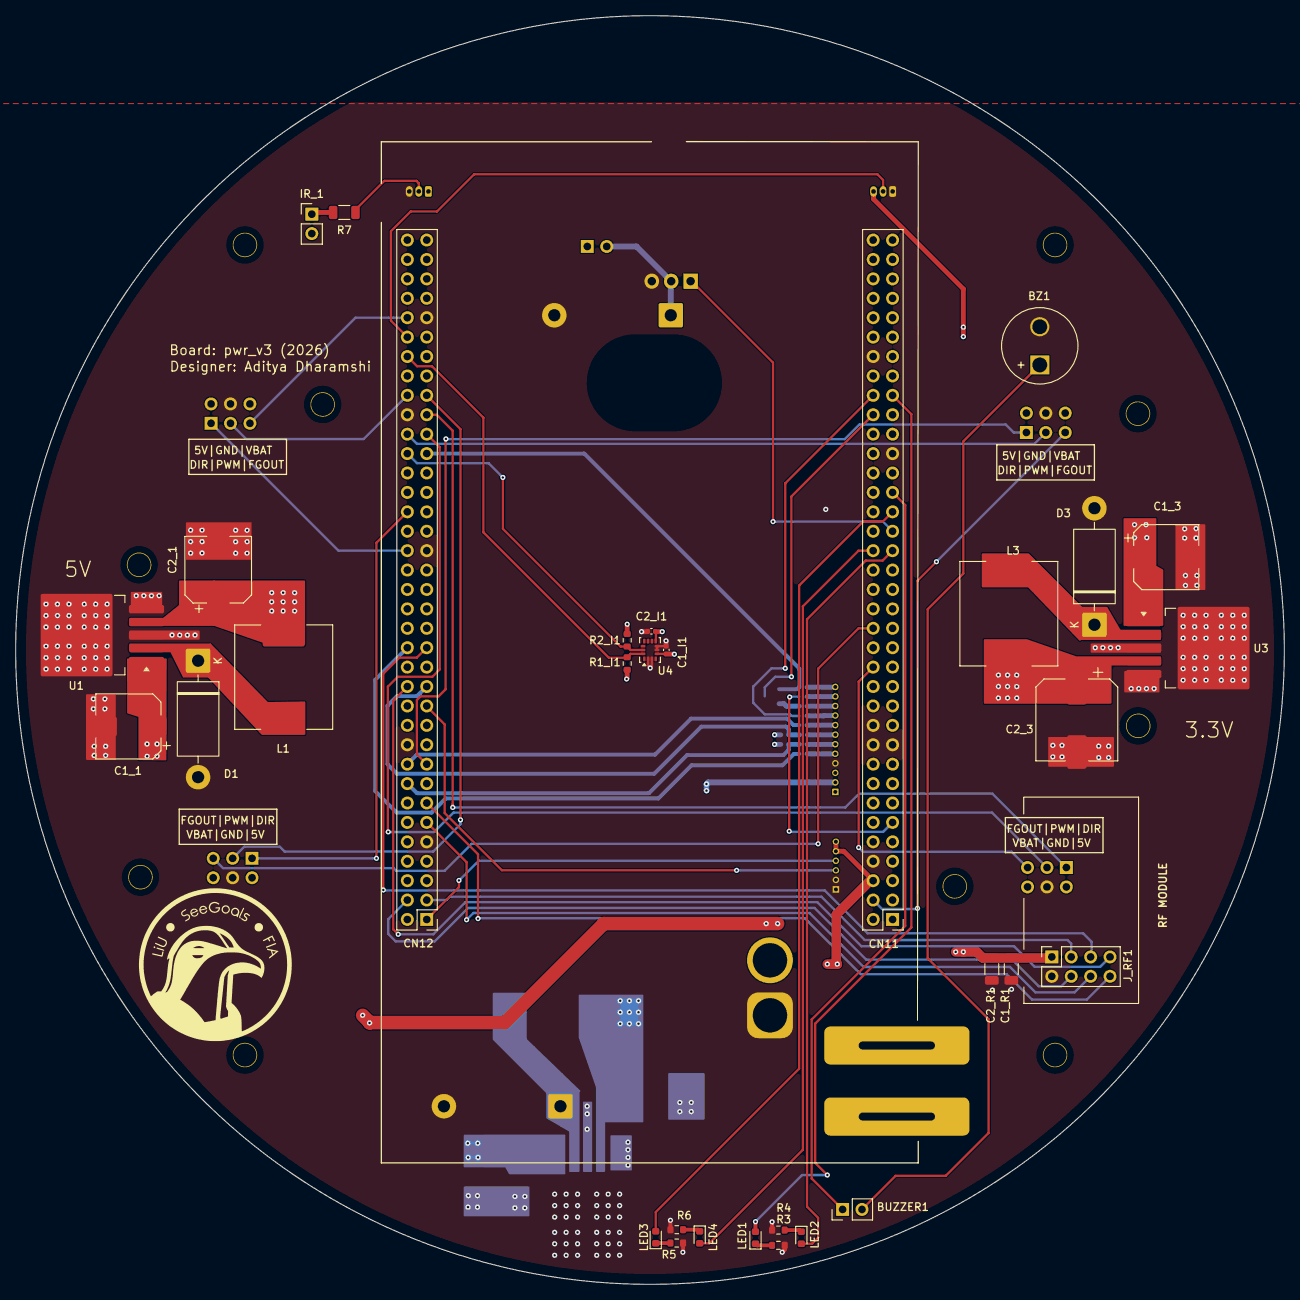
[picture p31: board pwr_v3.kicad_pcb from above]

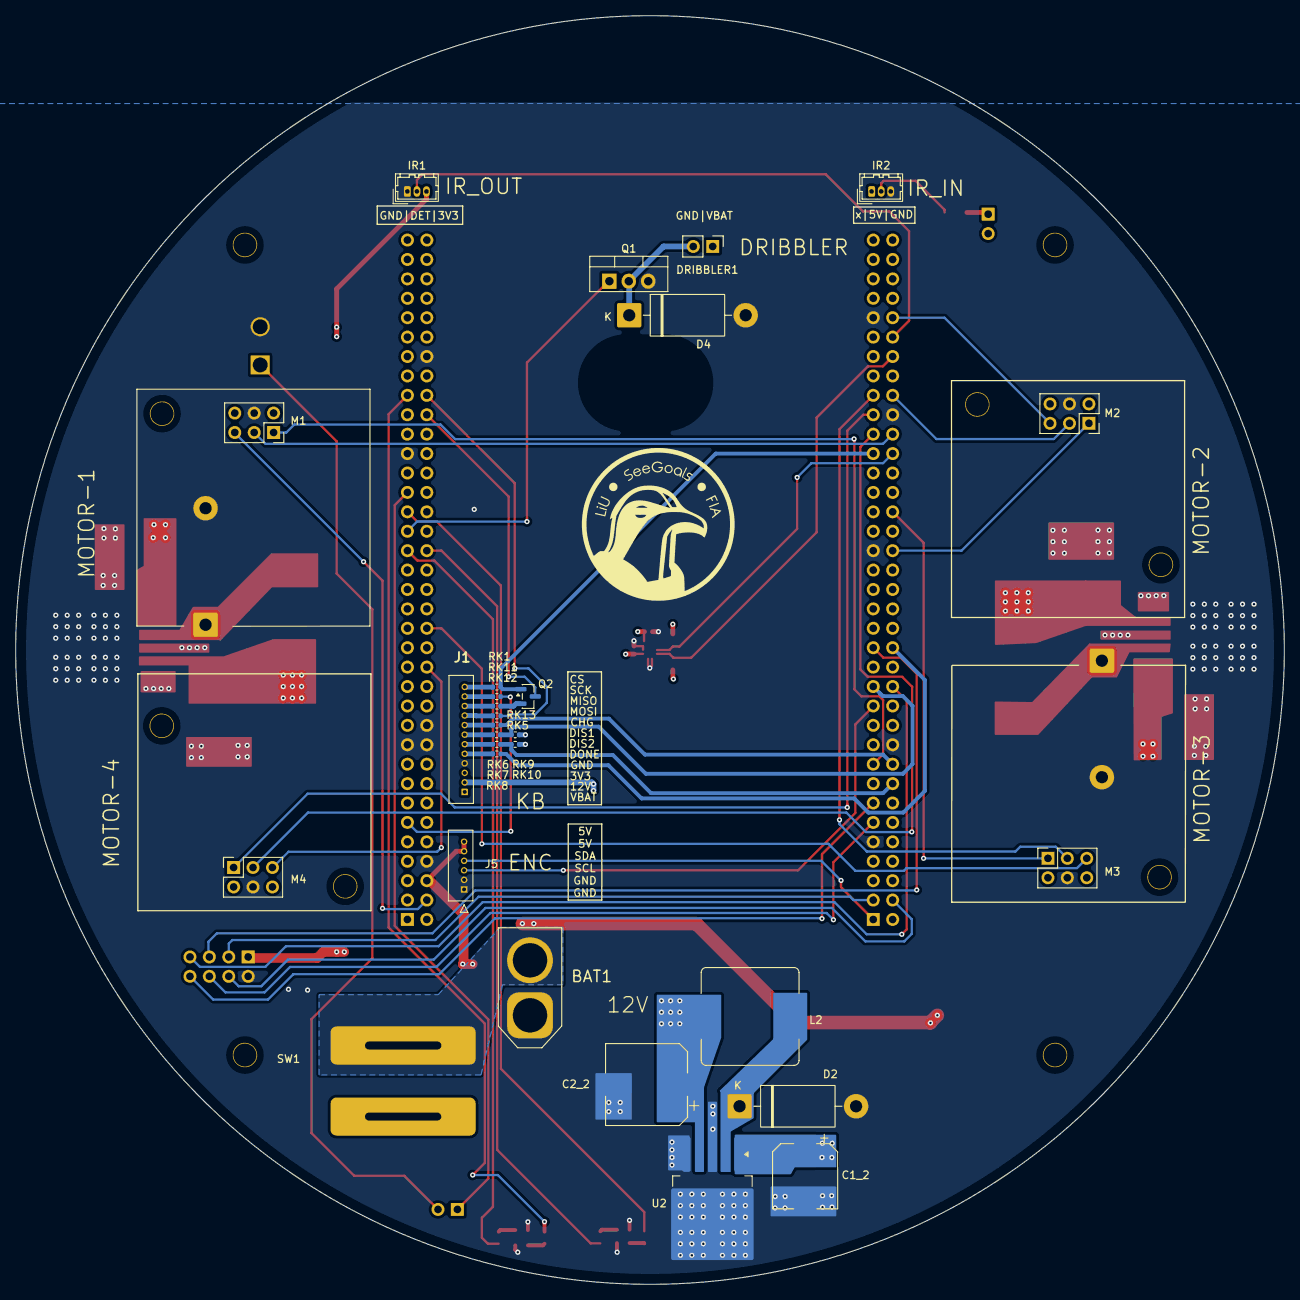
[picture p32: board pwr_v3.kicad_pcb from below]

Board: 4 copper layers, 166.0 x 166.0 mm, 71 parts (29 on the bottom side), 63 nets.

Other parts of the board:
MH1, MH2, MH3, MH4: (no value)
MH_11, MH_21, MH_22, MH_31, MH_41, MH_42: (no value)

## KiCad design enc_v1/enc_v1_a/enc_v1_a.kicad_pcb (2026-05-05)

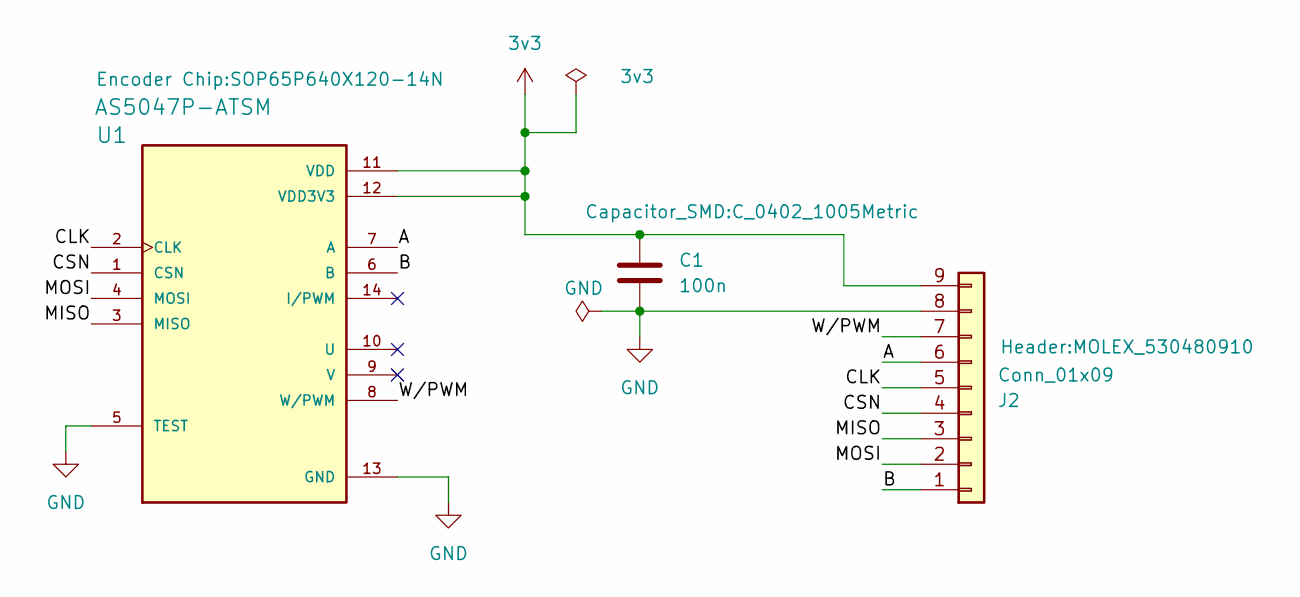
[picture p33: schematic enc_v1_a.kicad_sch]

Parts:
C1: 100n; C_0402_1005Metric
J2: Conn_01x09; MOLEX_530480910
U1: AS5047P-ATSM; SOP65P640X120-14N; PARTREV 1-01

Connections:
3v3: C1.1, J2.9, U1.11 (VDD), U1.12 (VDD3V3)
/A: J2.6, U1.7 (A)
/B: J2.1, U1.6 (B)
/CLK: J2.5, U1.2 (CLK)
/CSN: J2.4, U1.1 (CSN)
/MISO: J2.3, U1.3 (MISO)
/MOSI: J2.2, U1.4 (MOSI)
/W/PWM: J2.7, U1.8 (W/PWM)
GND: C1.2, J2.8, U1.5 (TEST), U1.13 (GND)

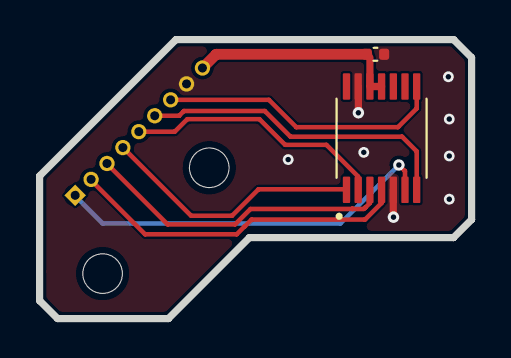
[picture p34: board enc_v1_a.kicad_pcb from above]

Board: 2 copper layers, 24.0 x 15.5 mm, 3 parts (1 on the bottom side), 9 nets.

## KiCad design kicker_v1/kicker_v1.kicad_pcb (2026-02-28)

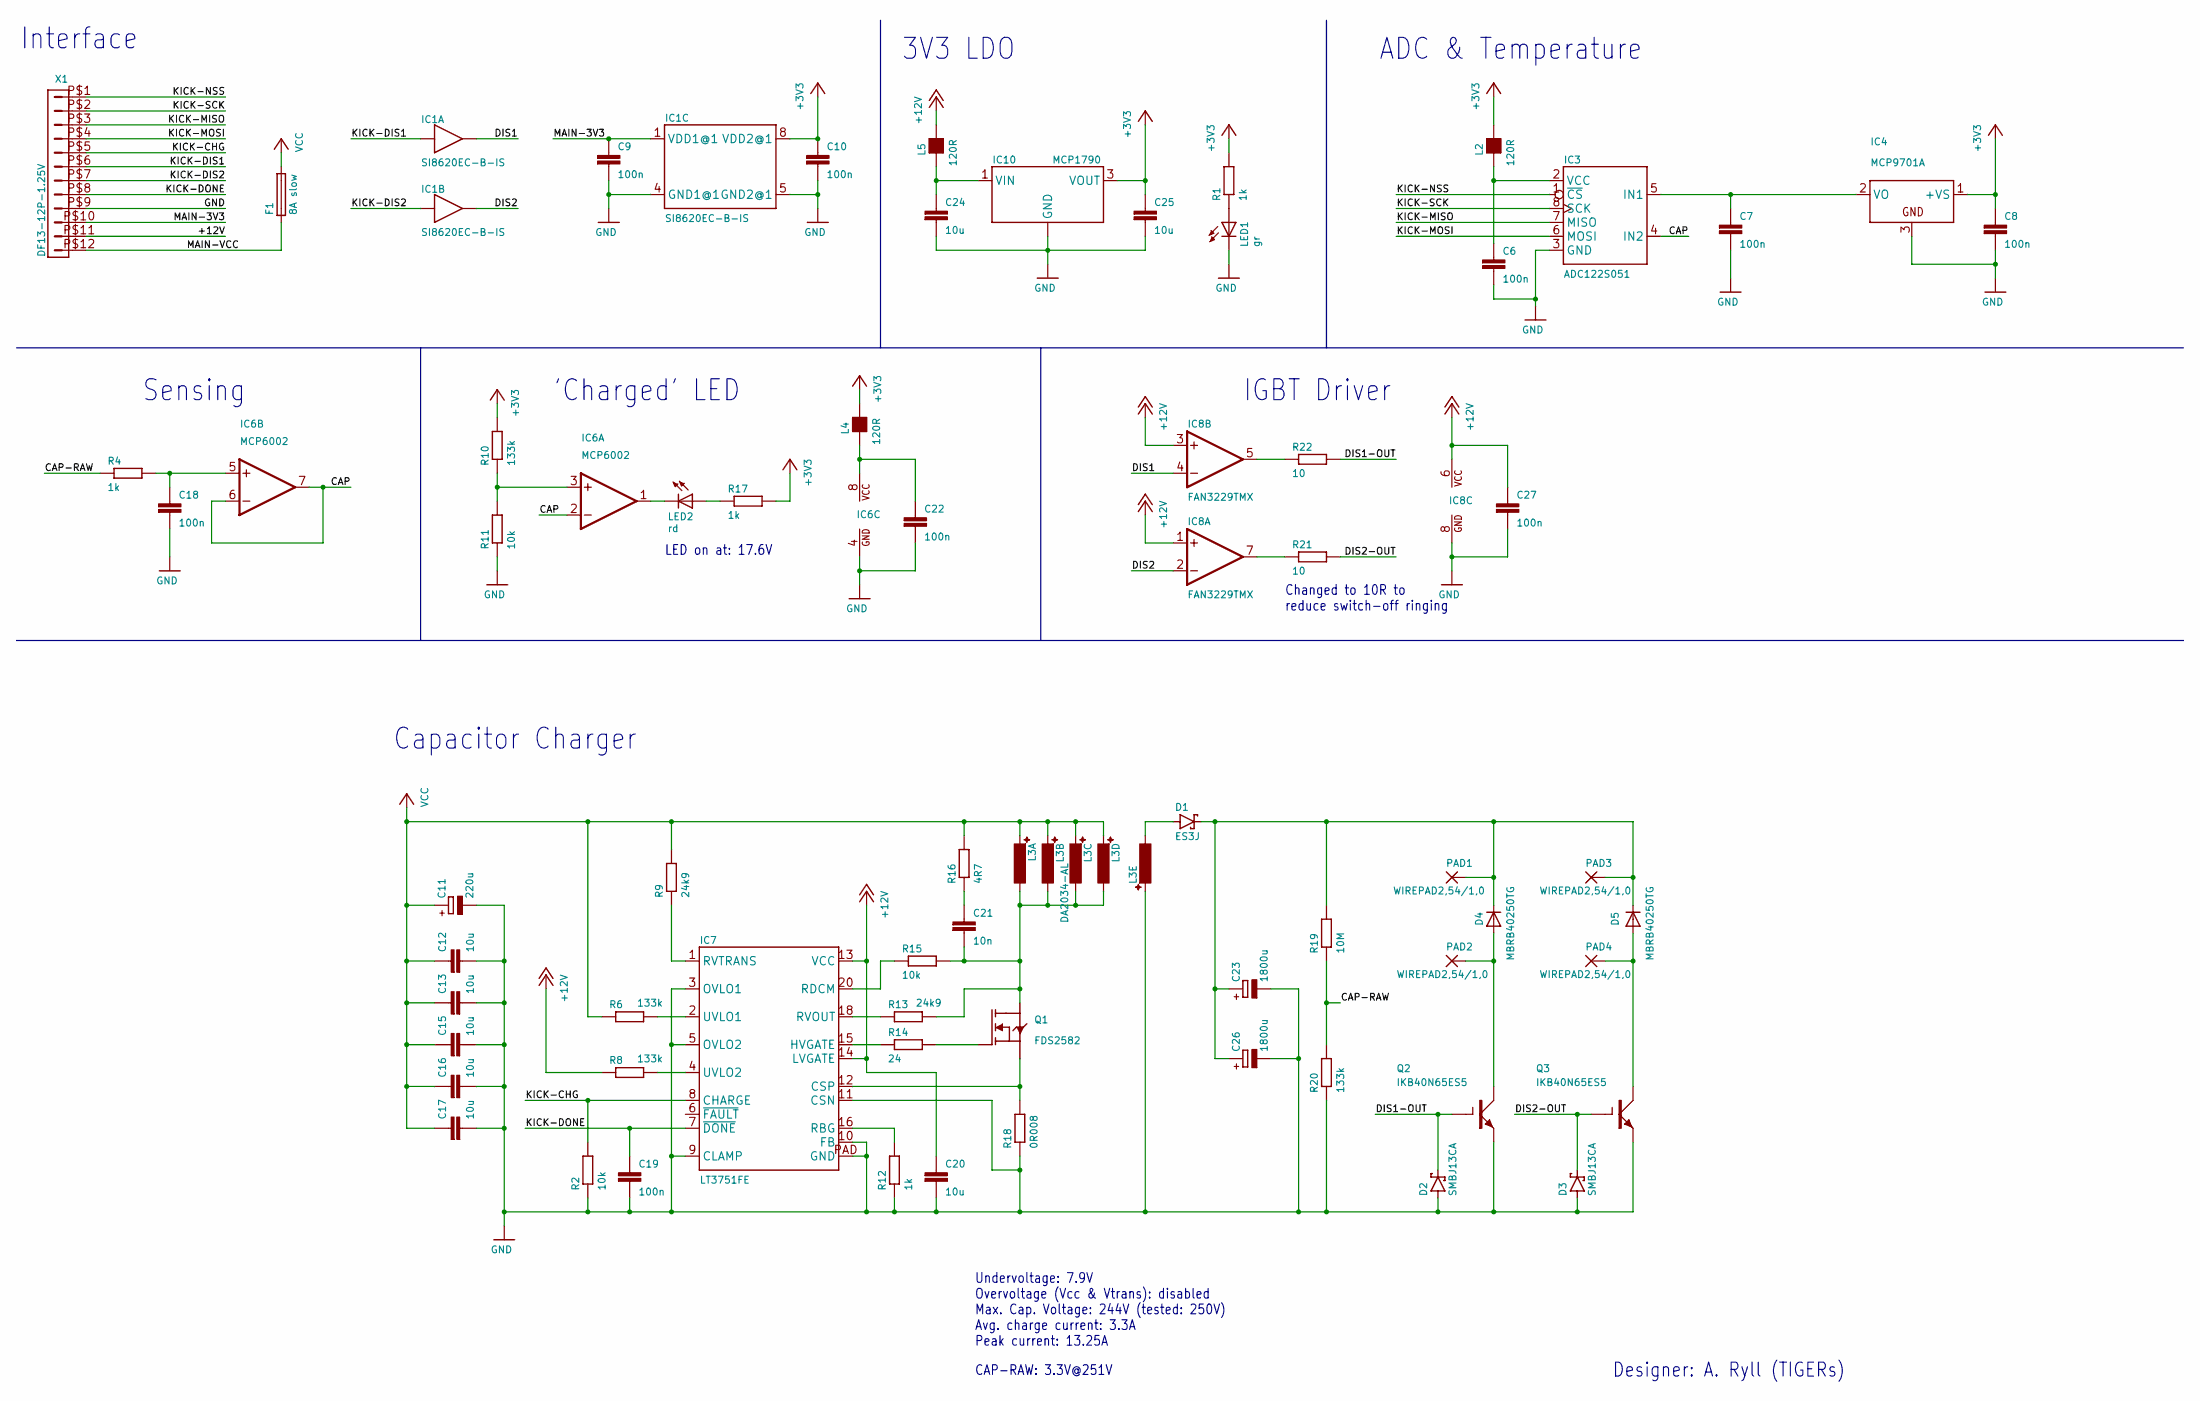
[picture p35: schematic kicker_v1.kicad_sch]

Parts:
C6, C7, C8, C9, C10, C18, C19, C22, C27: 100n; C0603; Digi-Key 1292-1397-1-ND
C11: 220u; PANASONIC_F; Mfg Part # EEEFT1H221AP; Digi-Key PCE5025CT-ND
C12, C13, C15, C16, C17: 10u; C1210; Mfg Part # C3225X5R1H106M250AB; Digi-Key 1276-6736-2-ND
C20, C24, C25: 10u; C0603; Digi-Key 490-12737-1-ND
C21: 10n; C0805
C23, C26: 1800u; EB35D; Digi-Key 493-7224-ND
D1: ES3J; SMC; Digi-Key ES3JCT-ND
D2, D3: SMBJ13CA; SMB; Digi-Key SMBJ13CA-FDICT-ND
D4, D5: MBRB40250TG; D2PAK; Digi-Key MBRB40250TGOS-ND
F1: 8A slow; 1206; Digi-Key 507-1194-1-ND
IC1: SI8620EC-B-IS; SOIC8N; Digi-Key 336-2062-5-ND
IC3: ADC122S051; MSOP8; Digi-Key ADC122S051CIMM/NOPBCT-ND
IC4: MCP9701A; SOT23; Digi-Key MCP9701AT-E/TTCT-ND
IC6: MCP6002; SOIC8N; Digi-Key MCP6002T-I/SNCT-ND
IC7: LT3751FE; TSSOP20P; Digi-Key LT3751EFE#PBF-ND
IC8: FAN3229TMX; SOIC8N; Digi-Key FAN3229TMXCT-ND
IC10: MCP1790; SOT223; Digi-Key MCP1790-3302E/DB-ND
L2, L4, L5: 120R; L0603; Digi-Key 490-1037-1-ND
L3: DA2034-AL; Mfg Part # DA2034-AL
LED1: gr; CHIP-LED0603; Digi-Key 732-4980-1-ND
LED2: rd; CHIP-LED0603; Digi-Key 732-4979-1-ND
PAD1, PAD2, PAD3, PAD4: WIREPAD2,54/1,0; 2,54_1,0
Q1: FDS2582; SOIC8N; Digi-Key FDS2582CT-ND
Q2, Q3: IKB40N65ES5; D2PAK; Digi-Key IKB40N65ES5ATMA1CT-ND
R1, R4, R12, R17: 1k; R0603; Digi-Key 311-1.00KHRCT-ND
R2, R11, R15: 10k; R0603; Digi-Key 311-10.0KHRCT-ND
R6, R8, R10, R20: 133k; R0603; Digi-Key P133KDBCT-ND
R9, R13: 24k9; R0603; Digi-Key P24.9KHCT-ND
R14: 24; R1206
R16: 4R7; R0805; Digi-Key RHM4.7KCT-ND
R18: 0R008; R1206; Digi-Key RHM.008ALCT-ND
R19: 10M; R1206; Digi-Key 541-10MBACT-ND
R21, R22: 10; R1206
X1: DF13-12P-1.25V; DF13C-12P-1.25V; Digi-Key H121957CT-ND

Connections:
+3V3: C8.1, C10.1, C25.1, IC1.8 (VDD2@1), IC4.1 (+VS), IC10.3 (VOUT), L2.2, L4.2, R1.2, R10.2, R17.2
+12V: C20.1, C27.1, IC7.13 (VCC), IC7.14 (LVGATE), IC8.1 (+IN), IC8.3 (+IN), IC8.6 (VCC), L5.2, R8.1, X1.P$11 (11)
CAP: IC3.4 (IN2), IC6.2 (-IN), IC6.6 (-IN), IC6.7 (OUT)
CAP-RAW: R4.1, R19.1, R20.2
CSP: IC7.12 (CSP), Q1.1 (S), Q1.2 (S), Q1.3 (S), R18.2
DIS1: IC1.7 (OUT), IC8.4 (-IN)
DIS1-OUT: D2.C, Q2.1 (G), R22.2
DIS1C: D4.1 (A), D4.3 (A), PAD2.1, Q2.2 (C); also elsewhere on the board
DIS2: IC1.6 (OUT), IC8.2 (-IN)
DIS2-OUT: D3.C, Q3.1 (G), R21.2
DIS2C: D5.1 (A), D5.3 (A), PAD4.1, Q3.2 (C); also elsewhere on the board
GND: C6.2, C7.2, C8.2, C9.2, C10.2, C11.-, C12.2, C13.2, C15.2, C16.2, C17.2, C18.2, C19.2, C20.2, C22.2, C23.-, C24.2, C25.2, C26.-, C27.2, D2.A, D3.A, IC1.4 (GND1@1), IC1.5 (GND2@1), IC3.3 (GND), IC4.3 (GND), IC6.4 (GND), IC7.3 (OVLO1), IC7.5 (OVLO2), IC7.9 (CLAMP), IC7.10 (FB), IC7.11 (CSN), IC7.PAD (GND), IC8.8 (GND), IC10.2 (GND), IC10.4 (GND), L3.12 (2), LED1.C, Q2.3 (E), Q3.3 (E), R2.1, R11.1, R12.1, R18.1, R20.1, X1.P$9 (9)
KICK-CHG: IC7.8 (CHARGE), R2.2, X1.P$5 (5)
KICK-DIS1: IC1.2 (IN), X1.P$6 (6)
KICK-DIS2: IC1.3 (IN), X1.P$7 (7)
KICK-DONE: C19.1, IC7.7 (~DONE), X1.P$8 (8)
KICK-MISO: IC3.7 (MISO), X1.P$3 (3)
KICK-MOSI: IC3.6 (MOSI), X1.P$4 (4)
KICK-NSS: IC3.1 (~CS), X1.P$1 (1)
KICK-SCK: IC3.8 (SCK), X1.P$2 (2)
LOUT: D1.A, L3.1
MAIN-3V3: C9.1, IC1.1 (VDD1@1), X1.P$10 (10)
MAIN-VCC: F1.1, X1.P$12 (12)
unnamed: IC8.7 (OUT), R21.1
unnamed: IC8.5 (OUT), R22.1
unnamed: C24.1, IC10.1 (VIN), L5.1
unnamed: C6.1, IC3.2 (VCC), L2.1
unnamed: C7.1, IC3.5 (IN1), IC4.2 (VO)
unnamed: LED1.A, R1.1
unnamed: C22.1, IC6.8 (VCC), L4.1
unnamed: IC6.3 (+IN), R10.1, R11.2
unnamed: C18.1, IC6.5 (+IN), R4.2
unnamed: LED2.A, R17.1
unnamed: IC6.1 (OUT), LED2.C
unnamed: IC7.16 (RBG), R12.2
unnamed: C21.1, R16.1
unnamed: Q1.4 (G), R14.2
unnamed: IC7.15 (HVGATE), R14.1
unnamed: IC7.18 (RVOUT), R13.1
unnamed: IC7.20 (RDCM), R15.1
unnamed: IC7.1 (RVTRANS), R9.1
unnamed: IC7.2 (UVLO1), R6.2
unnamed: IC7.4 (UVLO2), R8.2
VCAP: C23.+, C26.+, D1.C, D4.2 (C), D5.2 (C), PAD1.1, PAD3.1, R19.2; also elsewhere on the board
VCC: C11.+, C12.1, C13.1, C15.1, C16.1, C17.1, F1.2, L3.3 (2), L3.4 (2), L3.5 (2), L3.6 (2), R6.1, R9.2, R16.2
VDRAIN: C21.2, L3.7 (1), L3.8 (1), L3.9 (1), L3.10 (1), Q1.5 (D), Q1.6 (D), Q1.7 (D), Q1.8 (D), R13.2, R15.2

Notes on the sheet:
Undervoltage: 7.9V Overvoltage (Vcc & Vtrans): disabled Max. Cap. Voltage: 244V (tested: 250V) Avg. charge current: 3.3A Peak current: 13.25A
Capacitor Charger
3V3 LDO
LED on at: 17.6V
Changed to 10R to reduce switch-off ringing
ADC & Temperature
Designer: A. Ryll (TIGERs)
Sensing
CAP-RAW: 3.3V@251V
Interface
IGBT Driver
'Charged' LED

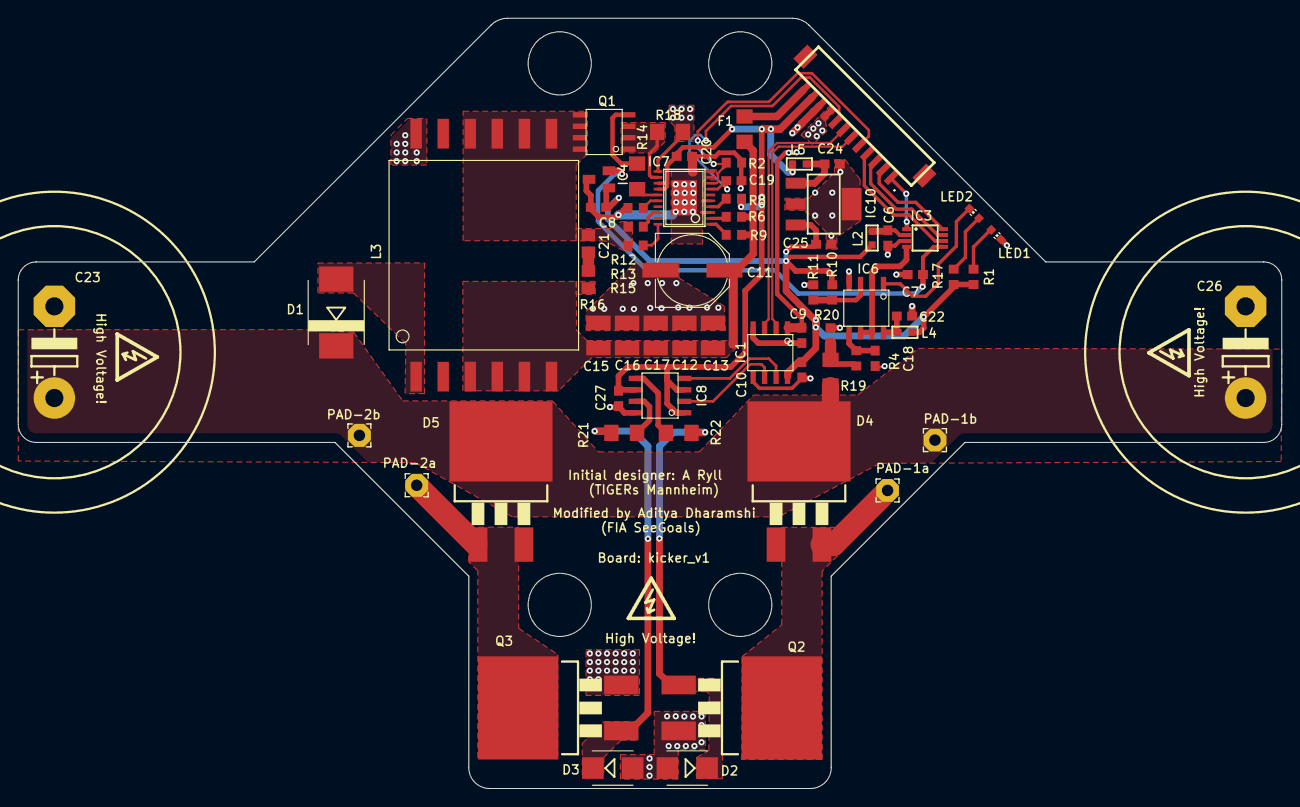
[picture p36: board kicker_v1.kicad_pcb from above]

Board: 2 copper layers, 140.0 x 85.3 mm, 71 parts (0 on the bottom side), 46 nets.

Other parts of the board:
PAD-1a, PAD-1b, PAD-2a, PAD-2b: 2,54_1,0
UNK_HOLE_0: dummyfp0
UNK_HOLE_1: dummyfp1
UNK_HOLE_2: dummyfp2
UNK_HOLE_3: dummyfp3

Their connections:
DIS1C: PAD-1a.1; also elsewhere on the board
DIS2C: PAD-2a.1; also elsewhere on the board
VCAP: PAD-1b.1, PAD-2b.1; also elsewhere on the board

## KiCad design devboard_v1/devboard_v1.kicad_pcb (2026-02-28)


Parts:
C1, C10, C16, C27, C30, C31: 4.7uF; C_0402_1005Metric; JLCPCB C23733
C2, C3, C4, C5, C6, C7, C8, C9, C12, C13, C14, C15, C17, C18, C19, C20, C21, C22, C23: 100nF; C_0402_1005Metric; JLCPCB C1525
C11: 1uF; C_0402_1005Metric; JLCPCB C14445
C24, C25, C26: 2.2uF; C_0402_1005Metric; JLCPCB C107369
C28, C29: 10uF; C_0402_1005Metric; JLCPCB C315248
CN11, CN12: Conn_02x36_Counter_Clockwise; PinHeader_2x35_P2.54mm_Vertical
D1: LED; LED_0603_1608Metric; JLCPCB C2286
IC1: ST1L05CPU33R; SON95P300X300X100-7N-D; Manufacturer_Part_Number ST1L05CPU33R; Mouser Part Number 511-ST1L05CPU33R
J1: Conn_01x08; PinSocket_1x08_P2.54mm_Vertical
R1: 62; R_0402_1005Metric; JLCPCB C412968
R2: 10k; R_0402_1005Metric; JLCPCB C71617
R3: 100k; R_0402_1005Metric; JLCPCB C191569
SW1: CK_KMS2xxG; TPS645-5NC105_JLCPCB; JLCPCB C19191549
U1: STM32H755ZITx; LQFP-144_20x20mm_P0.5mm; JLCPCB C730212

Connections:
/3V3: C1.1, C2.1, C3.1, C4.1, C5.1, C6.1, C7.1, C8.1, C9.1, C10.1, C11.1, C12.1, C13.1, C14.1, C15.1, C16.1, C17.1, C18.1, C19.1, C20.1, C21.1, C22.1, C27.1, C29.1, C30.1, C31.1, CN11.5, IC1.4 (VO), IC1.5 (V_O_SENSE), J1.1, R2.1, U1.7 (VDD), U1.8 (VBAT), U1.13 (VDD), U1.19 (VDD), U1.32 (VDD), U1.35 (VREF+), U1.36 (VDDA), U1.42 (VDD), U1.56 (VDD), U1.70 (VDDLDO), U1.71 (VDD), U1.79 (VDD), U1.92 (VDD), U1.105 (VDDLDO), U1.106 (VDD), U1.119 (VDD), U1.129 (VDD), U1.142 (PDR_ON), U1.143 (VDDLDO), U1.144 (VDD)
/5V_EXT: C28.1, CN11.6, IC1.1 (EN), IC1.6 (VI)
/BOOT0(1): CN11.7, R3.1, U1.135 (BOOT0)
/NRST: C23.1, CN11.14, J1.6, R2.2, SW1.3, SW1.4, U1.27 (NRST)
/PA0: CN11.28, U1.37 (PA0)
/PA1: CN11.30, U1.38 (PA1)
/PA2: CN12.35, U1.39 (PA2)
/PA3: CN12.37, U1.40 (PA3)
/PA4: CN11.32, U1.43 (PA4)
/PA5: CN12.11, U1.44 (PA5)
/PA6: CN12.13, U1.45 (PA6)
/PA7: CN12.15, U1.46 (PA7)
/PA8: CN12.23, U1.97 (PA8)
/PA9: CN12.21, U1.98 (PA9)
/PA10: CN12.33, U1.99 (PA10)
/PA11: CN12.14, U1.100 (PA11)
/PA12: CN12.12, U1.101 (PA12)
/PA15: CN11.17, U1.108 (PA15)
/PB0: CN11.34, R1.1, U1.49 (PB0)
/PB1: CN12.24, U1.50 (PB1)
/PB2: CN12.22, U1.51 (PB2)
/PB4: CN12.27, U1.131 (PB4)
/PB5: CN12.29, U1.132 (PB5)
/PB6: CN12.17, U1.133 (PB6)
/PB7: CN11.21, U1.134 (PB7)
/PB8: CN12.3, U1.136 (PB8)
/PB9: CN12.5, U1.137 (PB9)
/PB10: CN12.25, U1.66 (PB10)
/PB11: CN12.18, U1.67 (PB11)
/PB12: CN12.16, U1.72 (PB12)
/PB13: CN12.30, U1.73 (PB13)
/PB14: CN12.28, U1.74 (PB14)
/PB15: CN12.26, U1.75 (PB15)
/PC0: CN11.38, U1.28 (PC0)
/PC1: CN11.36, U1.29 (PC1)
/PC2: CN11.35, U1.30 (PC2_C)
/PC3: CN11.37, U1.31 (PC3_C)
/PC4: CN12.34, U1.47 (PC4)
/PC5: CN12.6, U1.48 (PC5)
/PC6: CN12.4, U1.93 (PC6)
/PC7: CN12.19, U1.94 (PC7)
/PC8: CN12.2, U1.95 (PC8)
/PC9: CN12.1, U1.96 (PC9)
/PC10: CN11.1, U1.109 (PC10)
/PC11: CN11.2, U1.110 (PC11)
/PC12: CN11.3, U1.111 (PC12)
/PC13: CN11.23, U1.9 (PC13)
/PC14: CN11.25, U1.10 (PC14)
/PC15: CN11.27, U1.11 (PC15)
/PD0: CN11.57, U1.112 (PD0)
/PD1: CN11.55, U1.113 (PD1)
/PD2: CN11.4, U1.114 (PD2)
/PD3: CN11.40, U1.115 (PD3)
/PD4: CN11.39, U1.116 (PD4)
/PD5: CN11.41, U1.117 (PD5)
/PD6: CN11.43, U1.120 (PD6)
/PD7: CN11.45, U1.121 (PD7)
/PD8: CN12.10, J1.7, U1.76 (PD8)
/PD9: CN11.69, J1.8, U1.77 (PD9)
/PD10: CN12.65, U1.78 (PD10)
/PD11: CN12.45, U1.81 (PD11)
/PD12: CN12.43, U1.82 (PD12)
/PD13: CN12.41, U1.83 (PD13)
/PD14: CN12.46, U1.84 (PD14)
/PD15: CN12.48, U1.85 (PD15)
/PE0: CN12.64, U1.138 (PE0)
/PE1: CN11.61, U1.139 (PE1)
/PE2: CN11.46, U1.1 (PE2)
/PE3: CN11.47, U1.2 (PE3)
/PE4: CN11.48, U1.3 (PE4)
/PE5: CN11.50, U1.4 (PE5)
/PE6: CN11.62, U1.5 (PE6)
/PE7: CN12.44, U1.57 (PE7)
/PE8: CN12.40, U1.58 (PE8)
/PE9: CN12.52, U1.59 (PE9)
/PE10: CN12.47, U1.60 (PE10)
/PE11: CN12.56, U1.61 (PE11)
/PE12: CN12.49, U1.62 (PE12)
/PE13: CN12.55, U1.63 (PE13)
/PE14: CN12.53, U1.64 (PE14)
/PE15: CN12.51, U1.65 (PE15)
/PF6: CN11.9, U1.20 (PF6)
/PF7: CN11.11, U1.21 (PF7)
/PF8: CN11.54, U1.22 (PF8)
/PF9: CN11.56, U1.23 (PF9)
/PF10: CN12.42, U1.24 (PF10)
/PF11: CN12.62, U1.52 (PF11)
/PF14: CN12.50, U1.53 (PF14)
/PF15: CN12.60, U1.54 (PF15)
/PG6: CN12.70, U1.86 (PG6)
/PG7: CN12.67, U1.87 (PG7)
/PG8: CN12.66, U1.88 (PG8)
/PG9: CN11.63, U1.122 (PG9)
/PG10: CN11.66, U1.123 (PG10)
/PG11: CN11.70, U1.124 (PG11)
/PG12: CN11.65, U1.125 (PG12)
/PG13: CN11.68, U1.126 (PG13)
/PG14: CN12.61, U1.127 (PG14)
/PH0: CN11.29, U1.25 (PH0)
/PH1: CN11.31, U1.26 (PH1)
/SWCLK: J1.3, U1.107 (PA14)
/SWDIO: J1.2, U1.102 (PA13)
/SWO: J1.5, U1.130 (PB3)
GND: C1.2, C2.2, C3.2, C4.2, C5.2, C6.2, C7.2, C8.2, C9.2, C10.2, C11.2, C12.2, C13.2, C14.2, C15.2, C16.2, C17.2, C18.2, C19.2, C20.2, C21.2, C22.2, C23.2, C24.2, C25.2, C26.2, C27.2, C28.2, C29.2, C30.2, C31.2, CN11.8, CN11.19, CN11.20, CN11.22, CN11.49, CN11.60, CN12.9, CN12.20, CN12.32, CN12.39, CN12.54, CN12.63, D1.1 (K), IC1.2 (GND), IC1.7 (EP), J1.4, R3.2, SW1.1, SW1.2, U1.6 (VSS), U1.12 (VSS), U1.14 (VSSSMPS), U1.18 (VSS), U1.33 (VSS), U1.34 (VSSA), U1.41 (VSS), U1.55 (VSS), U1.69 (VSS), U1.80 (VSS), U1.89 (VSS), U1.104 (VSS), U1.118 (VSS), U1.128 (VSS), U1.141 (VSS)
unnamed: C24.1, U1.68 (VCAP)
unnamed: C25.1, U1.103 (VCAP)
unnamed: C26.1, U1.140 (VCAP)
unnamed: D1.2 (A), R1.2

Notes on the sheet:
VddA - P36
STLink Connection SWDIO -> PA13 SWCLK -> PA14 SWO -> PB3 UART_TX -> PD8 UART_RX -> PD9 STLINK-V3MINIE is a good choice
Vref+ P35
Reset button
One 100nF cap for every Vdd LDO pin, connect to 3.3V P70,105,143
This is to evaluate the custom circuit of STM32H755ZI chip. Board pinouts are similar to the Nucleo H7555ZI.
One 100nF cap for every Vdd pin (13 pins), connect to 3.3V


Board: 4 copper layers, 70.0 x 95.0 mm, 41 parts (0 on the bottom side), 108 nets.

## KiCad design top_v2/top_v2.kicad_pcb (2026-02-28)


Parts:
C1: 8.2pF; C_0603_1608Metric; JLCPCB Part C71660
C2: 0.1uF; C_1206_3216Metric; JLCPCB Part C2981728
C3: 10uF; C_1206_3216Metric; JLCPCB Part C696375
CN7: Conn_02x10_Counter_Clockwise; PinHeader_2x10_P2.54mm_Vertical
CN8: Conn_02x08_Odd_Even; PinHeader_2x08_P2.54mm_Vertical
J_RF1: Conn_02x04_Counter_Clockwise; PinSocket_2x04_P2.54mm_Vertical; JLCPCB Part C2977588

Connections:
/3V3: C1.1, C2.1, C3.1, CN8.7, J_RF1.1
/CE: CN7.1, J_RF1.4
/CSN: CN7.2, J_RF1.3
/GND: C1.2, C2.2, C3.2, CN7.8, CN8.11, CN8.13, J_RF1.2
/IRQ: CN7.20, J_RF1.7
/MISO: CN7.12, J_RF1.8
/MOSI: CN7.13, J_RF1.5
/SCK: CN7.10, J_RF1.6

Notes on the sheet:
Three decaps are placed, two are the regular 0.1uF and 10uF. 8.2pF is specifically for reducing noise at 2.4GHz
This board interfaces the nRF to H536ZI devboard, mainly for basestation
H536ZI header pinouts from datasheet
Pin mappings


Board: 2 copper layers, 60.0 x 35.0 mm, 6 parts (0 on the bottom side), 8 nets.

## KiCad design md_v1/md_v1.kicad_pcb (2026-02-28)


Board: 2 copper layers, 30.5 x 31.0 mm, 20 parts (1 on the bottom side), 24 nets.

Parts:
C1: 100nF; C_0402_1005Metric
C2: 47nF; C_0402_1005Metric
C3, C7: 1uF; C_0402_1005Metric
C4: 0u1F; C_0402_1005Metric
C5: 22uF; C_2220_5750Metric
C6: 22uF; C_0402_1005Metric
L1: 47uH; L_0805_2012Metric
MH1, MH2: (no value)
MOTOR1: Conn_01x08; PinHeader_1x08_P2.54mm_Vertical
POWER1: Conn_02x03_Odd_Even; PinHeader_2x03_P2.54mm_Vertical
R1, R2: 5k1; R_0603_1608Metric
R3: 27k; R_0603_1608Metric
R4: 20k; R_0603_1608Metric
R5: 1M; R_0805_2012Metric
R6: 47k; R_0402_1005Metric
R7: 22k; R_0402_1005Metric
U1: MCT8316Z0TRGFR; RGF0040E-IPC_A

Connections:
/5V: POWER1.5, R1.1, R2.1
/AVDD: C7.1, R3.1, R5.2, R6.2, U1.23 (NSLEEP), U1.25 (AVDD), U1.33 (MODE)
/DIR: POWER1.6, U1.36 (DIR)
/FGOUT: POWER1.2, R2.2, U1.40 (FGOUT)
/GND_BK: C6.2, MOTOR1.4, U1.4 (GND_BK)
/H1: MOTOR1.6, U1.27 (HPA)
/H2: MOTOR1.5, U1.29 (HPB)
/H3: MOTOR1.7, U1.31 (HPC)
/PWM: POWER1.4, U1.39 (PWM)
/SW_BK: C6.1, L1.2, MOTOR1.8, U1.3 (FB_BK)
/U: MOTOR1.1, U1.13 (OUTA_1), U1.14 (OUTA_2)
/V: MOTOR1.2, U1.16 (OUTB_1), U1.17 (OUTB_2)
/Vbat: C3.2, C4.1, C5.1, POWER1.1, U1.9 (VM_1), U1.10 (VM_2), U1.11 (VM_3)
/W: MOTOR1.3, U1.19 (OUTC_1), U1.20 (OUTC_2)
/nFault: R1.2, U1.22 (NFAULT)
GND: C1.2, C4.2, C5.2, C7.2, POWER1.3, R4.2, R7.2, U1.2 (AGND_1), U1.12 (PGND_1), U1.15 (PGND_2), U1.18 (PGND_3), U1.21 (DRVOFF), U1.26 (AGND_2), U1.38 (BRAKE), U1.41 (EP)
unnamed: R7.1, U1.35 (ADVANCE)
unnamed: C3.1, U1.8 (CP)
unnamed: C2.1, U1.7 (CPH)
unnamed: C2.2, U1.6 (CPL)
unnamed: C1.1, R3.2, R4.1, U1.37 (ILIM)
unnamed: R6.1, U1.34 (SLEW)
unnamed: L1.1, U1.5 (SW_BK)
unnamed: R5.1, U1.24 (VSEL_BK)

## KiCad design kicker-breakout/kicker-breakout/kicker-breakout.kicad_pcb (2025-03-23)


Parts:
J1: 1x04_P2.54mm; Molex_KK-254_AE-6410-04A_1x04_P2.54mm_Vertical
J2: 1x08_P2.54mm; Molex_KK-254_AE-6410-08A_1x08_P2.54mm_Vertical
J3: DF13C_CL535-0412-6-51_1x12-1MP_P1.25mm_Vertical; Hirose_DF13C_CL535-0412-6-51_1x12-1MP_P1.25mm_Vertical
Q1: BSS84; SOT-23
RN7A1, RN7B1, RN7C1, RN7D1, RN8A1, RN8B1, RN8C1, RN8D1: 100; R_0805_2012Metric_Pad1.20x1.40mm_HandSolder
RN9A1, RN9D1: 10k; R_0805_2012Metric_Pad1.20x1.40mm_HandSolder

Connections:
+3V3: J1.3, J3.10, RN9A1.2, RN9D1.2
+12V: J1.2, J3.11
/KICK_CHG: J2.5, RN7A1.1
/KICK_CLK: J2.2, RN8B1.1
/KICK_CS: J2.1, Q1.1 (G), RN8A1.1
/KICK_DIS1: J2.6, RN7B1.1, RN9A1.1
/KICK_DIS2: J2.7, RN7C1.1, RN9D1.1
/KICK_ERR: J2.8, RN7D1.1
/KICK_MISO: J2.3, Q1.3 (D)
/KICK_MOSI: J2.4, RN8D1.1
GND: J1.4, J3.9
unnamed: J3.1, RN8A1.2
unnamed: J3.2, RN8B1.2
unnamed: J3.3, RN8C1.2
unnamed: J3.4, RN8D1.2
unnamed: J3.5, RN7A1.2
unnamed: J3.6, RN7B1.2
unnamed: J3.7, RN7C1.2
unnamed: J3.8, RN7D1.2
unnamed: Q1.2 (S), RN8C1.1
VCC: J1.1, J3.12

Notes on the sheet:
POWER
KICKER_CONNECTION
DEVBOARD


Board: 2 copper layers, 44.0 x 37.8 mm, 14 parts (0 on the bottom side), 21 nets.

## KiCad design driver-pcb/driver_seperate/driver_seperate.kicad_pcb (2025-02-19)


Board: 4 copper layers, 37.8 x 34.2 mm, 21 parts (0 on the bottom side), 23 nets.

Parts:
C1: 100nF; C_0805_2012Metric
C2: 47nF; CAPC3216X180N
C3, C7: 1uF; CAPC3216X178N
C4: 0u1F; CAPC1608X95N
C5: KCM55TR71H226MH01L; CAPC6153X500N
C6: 22uF; C_1206_3216Metric
H1, H2: MountingHole; MountingHole_2.2mm_M2
IC1: MCT8316Z0TQRGFRQ1; QFN50P500X700X100-41N-D
J2: Motor; Molex_KK-254_AE-6410-08A_1x08_P2.54mm_Vertical
J3: Connector_PinSocket_2.54mm:PinSocket_2x03_P2.54mm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; PinSocket_2x03_P2.54mm_Vertical
J4: Connector_Molex:Molex_KK-396_5273-02A_1x02_P3.96m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; Molex_KK-396_5273-02A_1x02_P3.96mm_Vertical
L1: 47uH; INDPM7973X540N
R1, R2: 5k1; R_0603_1608Metric_Pad0.98x0.95mm_HandSolder
R3: 1M; R_0805_2012Metric_Pad1.20x1.40mm_HandSolder
R4: 27k; R_0603_1608Metric_Pad0.98x0.95mm_HandSolder
R5: 20k; R_0603_1608Metric_Pad0.98x0.95mm_HandSolder
R6: 47k; R_0402_1005Metric_Pad0.72x0.64mm_HandSolder
R7: 22k; R_0402_1005Metric_Pad0.72x0.64mm_HandSolder

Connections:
/Motor Driver/AVDD: C7.1, IC1.23 (NSLEEP), IC1.25 (AVDD), IC1.33 (MODE), R1.1, R2.1, R3.2, R4.1, R6.2, R7.2
/Motor Driver/BRAKE: IC1.38 (BRAKE), J3.2
/Motor Driver/DIR: IC1.36 (DIR), J3.3
/Motor Driver/FGOUT: IC1.40 (FGOUT), J3.4, R2.2
/Motor Driver/H1: IC1.27 (HPA), J2.6 (H1)
/Motor Driver/H2: IC1.29 (HPB), J2.5 (H2)
/Motor Driver/H3: IC1.31 (HPC), J2.7 (H3)
/Motor Driver/PWM: IC1.39 (PWM), J3.5
/Motor Driver/SW_BK: C6.1, IC1.3 (FB_BK), J2.8 (SW_BK), L1.2
/Motor Driver/U: IC1.13 (OUTA_1), IC1.14 (OUTA_2), J2.1 (U)
/Motor Driver/V: IC1.16 (OUTB_1), IC1.17 (OUTB_2), J2.2 (V)
/Motor Driver/VM: C3.2, C4.1, C5.1, IC1.9 (VM_1), IC1.10 (VM_2), IC1.11 (VM_3), J4.1
/Motor Driver/W: IC1.19 (OUTC_1), IC1.20 (OUTC_2), J2.3 (W)
/Motor Driver/nFault: IC1.22 (NFAULT), J3.1, R1.2
GNDREF: C1.2, C4.2, C5.2, C6.2, C7.2, IC1.2 (AGND_1), IC1.4 (GND_BK), IC1.12 (PGND_1), IC1.15 (PGND_2), IC1.18 (PGND_3), IC1.21 (DRVOFF), IC1.26 (AGND_2), IC1.41 (EP), J2.4 (GND_BK), J4.2, R5.2
unnamed: IC1.35 (ADVANCE), R7.1
unnamed: C3.1, IC1.8 (CP)
unnamed: C2.1, IC1.7 (CPH)
unnamed: C2.2, IC1.6 (CPL)
unnamed: C1.1, IC1.37 (ILIM), R4.2, R5.1
unnamed: IC1.34 (SLEW), R6.1
unnamed: IC1.5 (SW_BK), L1.1
unnamed: IC1.24 (VSEL_BK), R3.1

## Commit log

2023-12-08 Initial design of driverboard
    [Connectors.kicad_sch, Devboard.kicad_sch, Driverboard.kicad_pcb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]
2023-12-20 Motor Driver complete
    [Connectors.kicad_sch, Controller.kicad_sch, Devboard.kicad_sch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]
2024-01-18 Powerboard v0.1, not ready for manufacturing yet
    [BMS.kicad_sch, Connectors.kicad_sch, Converters.kicad_sch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]
2024-01-29 DriverboardComp is the complete design, need to be evaluated
    [BMS.kicad_sch, Connectors.kicad_sch, Converters.kicad_sch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]
2024-04-10 TempBoard is the current version
    [BMS.kicad_sch, Connectors.kicad_sch, Converters.kicad_sch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]
2024-04-10 Devboard ports defined
    [BMS.kicad_sch, Connectors.kicad_sch, Converters.kicad_sch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]
2024-08-04 version 1 imu with added led
    [powerboard_L6981.kicad_pcb, powerboard_L6981.kicad_sch]
2024-08-16 re-add imu v1
    [bom.csv, designators.csv, imu_LSM6DSL.kicad_pcb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]
2025-01-20 Deleted imu version that doesn't work
    [imu_LSM6DSL.kicad_pcb, imu_LSM6DSL.kicad_sch]
2025-01-29 Copy Kicker to to the main
    [Kicking Device v13b.brd, Kicking Device v13b.kicad_pcb, Kicking Device v13b.kicad_sch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]
2025-02-19 Add driver pcb (#4)
    * Add driver pcb layout, libraries, simplify schematic
    * remove bloat
    * Minor pcb changes
    * Add backups?
    * Thing
    * Add finished pcb
    * Add gerbers and backups
    * Add newest version, revision started
    * Add start of new design
    * Add new design
    * Add screw holes
    * Small U,V,W width change
    * Add libs
    * Add pcb v2, Remove old files
    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
    [controller.kicad_sch, driver_seperate.kicad_pcb, driver_seperate.kicad_sch]
2025-02-19 Move driver pcb to seperate folder
    [controller.kicad_sch, driver_seperate.kicad_pcb, driver_seperate.kicad_sch]
2025-03-22 Add kicker breakout board
    [kicker-breakout.kicad_pcb, kicker-breakout.kicad_sch]
2025-03-23 Add jlpcb design rules and fix incorrect pullup value
    [kicker-breakout.kicad_pcb, kicker-breakout.kicad_sch]
2025-03-23 Add production files
    [bom.csv, designators.csv, positions.csv]
2025-05-19 Power board v2 finalized files
    [471005264152 (rev1).stp, bom.csv, designators.csv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]
2025-05-19 Motor driver PCB finalized files
    [bom.csv, designators.csv, md_v1.csv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]
2025-11-03 Kicker board updated files uploaded
    [K_order.xls, designators.csv, kickerBoard.step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]
2026-02-28 File structure enhanced.
    Added uniform titleblocks and 3D renders for easier view, file cleanups.
    [K_order.xls, bom.csv, designators.csv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]
2026-05-05 Encoder files added.
    There are two mirrored versions a and b
    [enc_v1_a.kicad_pcb, enc_v1_a.kicad_sch, enc_v1_b.kicad_pcb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]
2026-05-15 pwr_v3 initial files added
    Planning to add an additional connector for encoder board, and fixing some connector issues.
    [471005264152 (rev1).stp, 530470610.stp, MCT8316Z0TQRGFRQ1.stp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]
2026-05-16 Schematic and layout updated
    Sch - Unwanted global labels removed from IMU, added new kicker labels, changed kicker connector footprint.
    Layout - Updated kicker and encoder positions, routing updated.
    [530471210.stp, imu.kicad_sch, kb.kicad_sch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]
2026-06-21 Finalized files
    Final files used for fabrication. Docs and Images added for easy view.
    [imu.kicad_sch, kb.kicad_sch, pwr_v3.kicad_pcb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]
